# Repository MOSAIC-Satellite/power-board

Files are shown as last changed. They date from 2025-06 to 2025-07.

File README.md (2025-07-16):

# Power Board

This is the repository for MOSAIC's Power Board.

For detailed information on the Power Board, check out its core documentation [here](https://www.mosaicsat.org/core_documentation/hardware/power_board/).

To get your own MOSAIC Power Board, visit the MOSAIC fabrication guide [here](https://www.mosaicsat.org/getting_mosaic/).

## Current Features

*Newest board version: 2.0*

| **Feature** |
| :----------- |
| 6x high-side DC sensors for solar cells |
| LiPo battery high side DC sensor |
| Single-cell LiPo battery charger circuit |
| 12x  2mm JST solar cell input jacks|
| 2x 2mm JST battery input jacks |
| LiPo battery overcharge protection |
| Solar cell reverse current protection |
| 2x Qwiic connectors for I2C connection to Main Board |

## Planned Changes

The following are the current plans for changes to MOSAIC's Power Board. 

- The current version of MOSAIC's Power Board is designed to be used with only a single-cell LiPo battery like [this one](https://www.sparkfun.com/lithium-ion-battery-2ah.html). Future iterations of the Power Board should include the option to utilize different energy storage methods, such as AA and 18650 batteries. This, of course, will require a different charger circuit for each method, so the board may include a new slot where users can plug in their preferred power charger circuit. 

## Change Log

You can find the change log for the Power Board on MOSAIC's website [here](https://www.mosaicsat.org/core_documentation/hardware/power_board/change_log/).

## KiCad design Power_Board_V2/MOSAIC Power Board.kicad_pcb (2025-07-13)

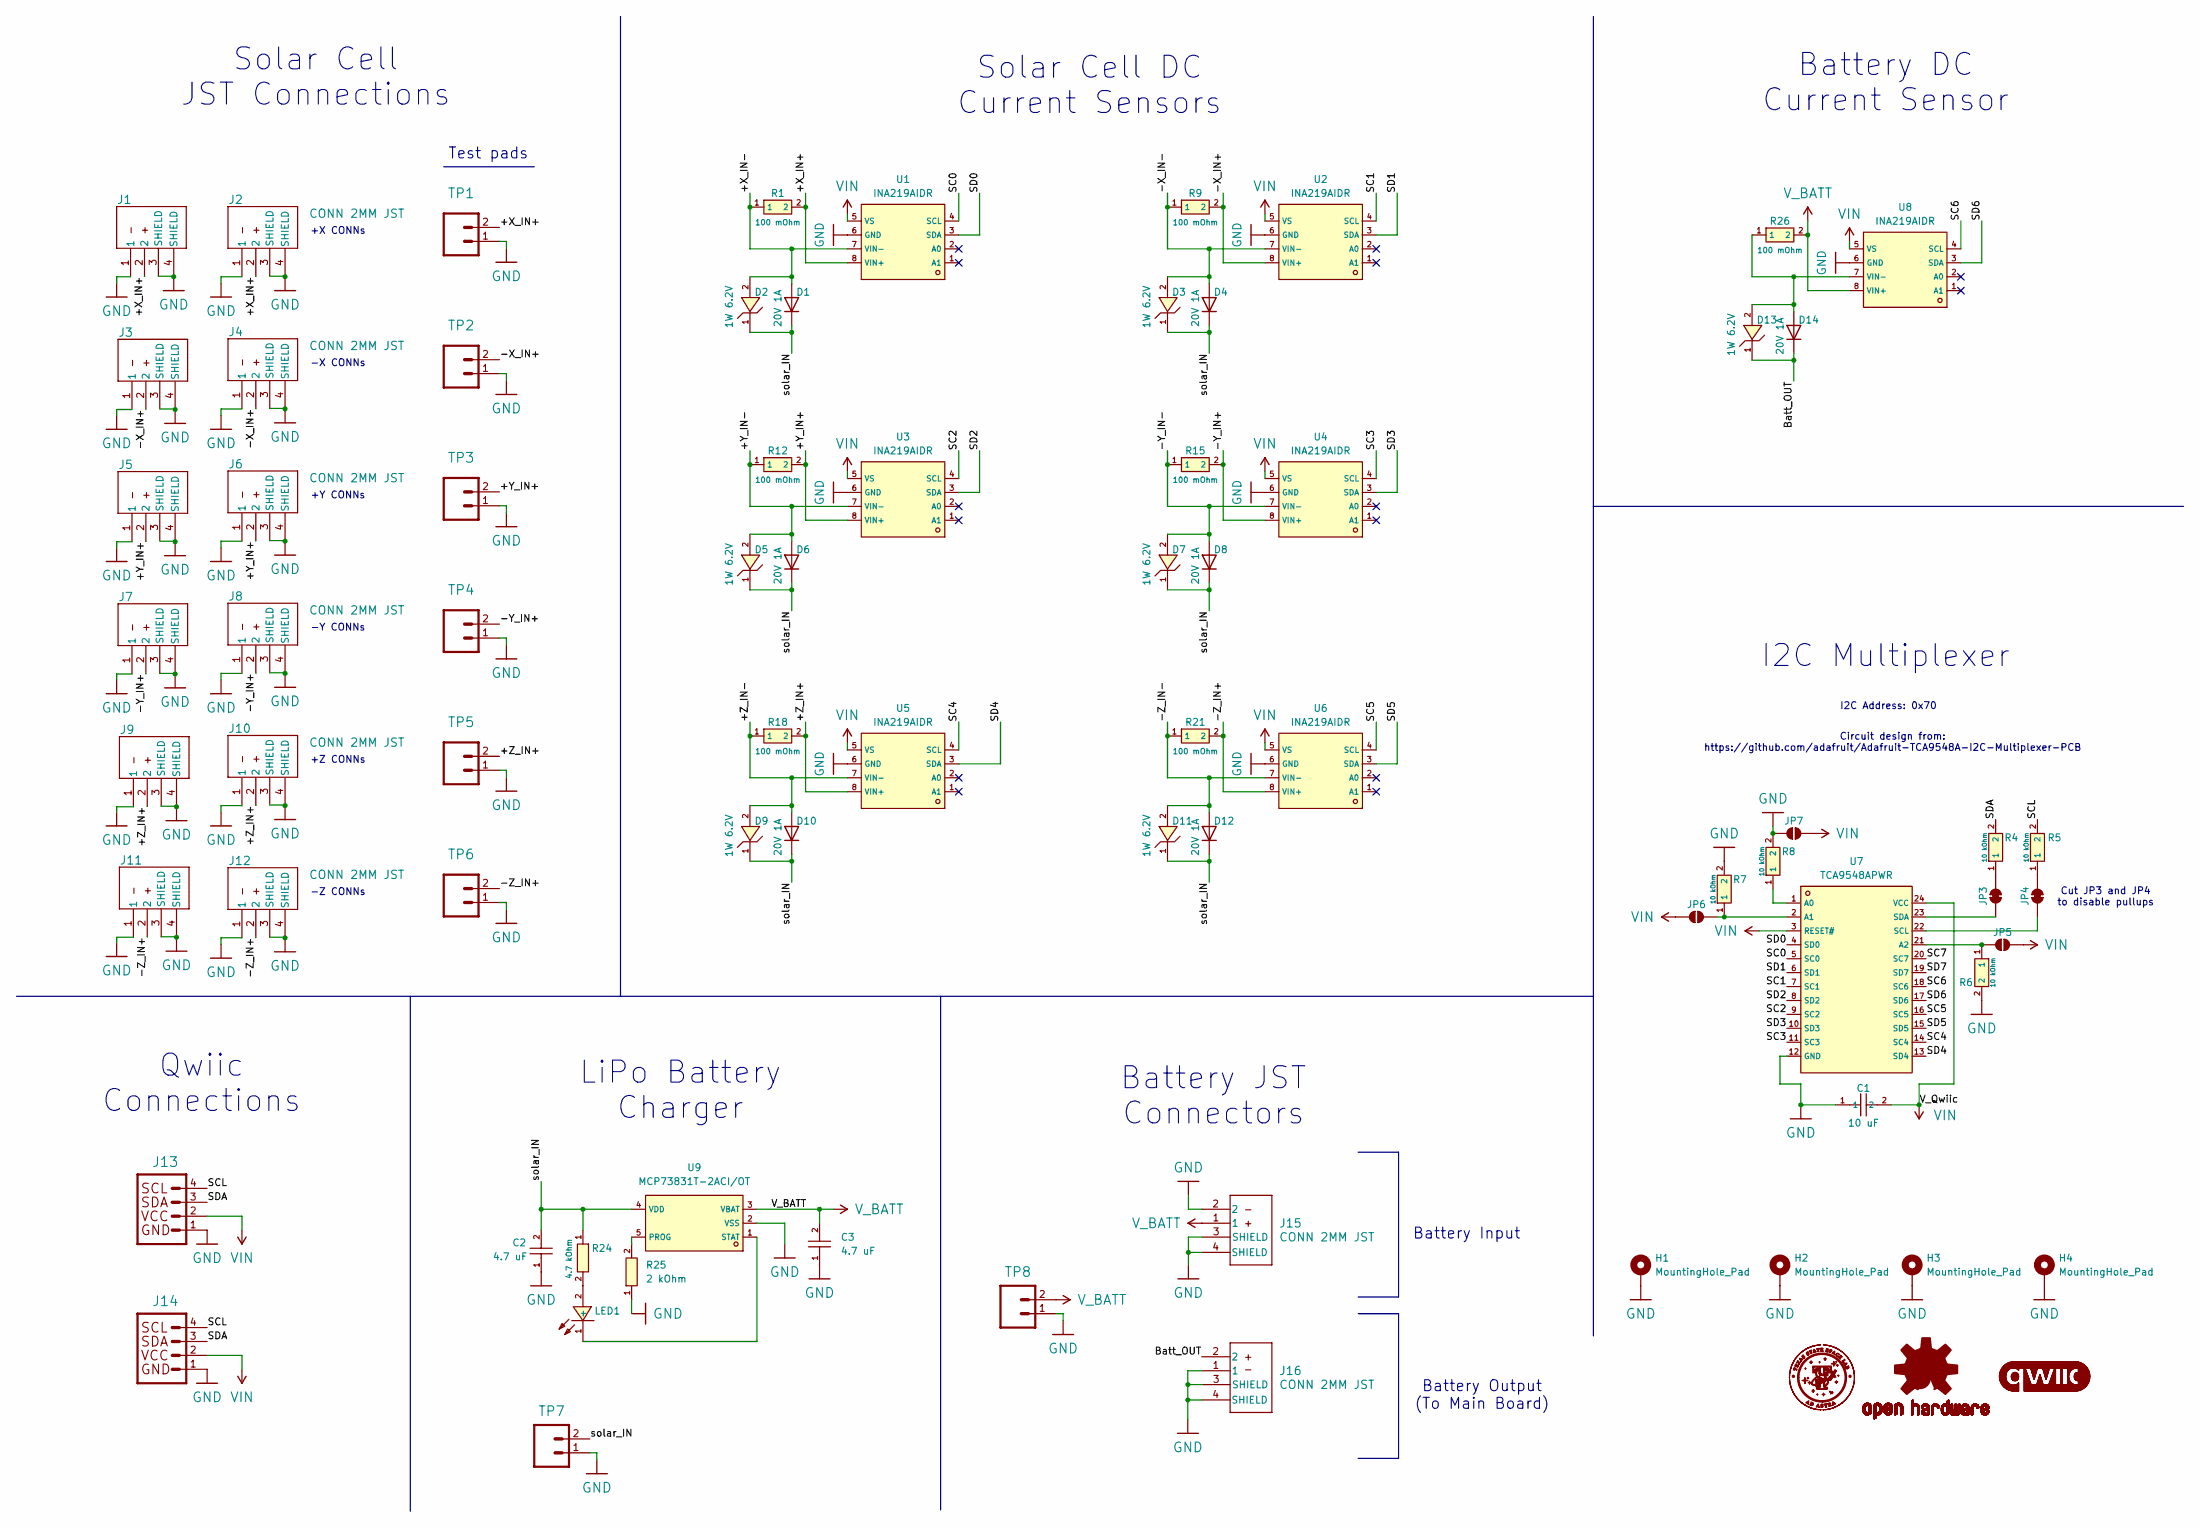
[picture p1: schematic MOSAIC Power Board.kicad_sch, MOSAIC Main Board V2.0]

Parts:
C1: 10 uF; C_0603; LCSC C1691
C2, C3: 4.7 uF; C_0603; LCSC C1705
D1, D4, D6, D8, D10, D12, D14: 20V 1A; D_SOD-323; JLCPCB Part # C41424805
D2, D3, D5, D7, D9, D11, D13: 1W 6.2V; Z_DO-214AC; LCSC C110527
H1, H2: MountingHole_Pad; MountingHole_3.2mm_Pad_Oval
H3, H4: MountingHole_Pad; MountingHole_3.2mm_M3_Pad
J1, J2, J3, J4, J5, J6, J7, J8, J9, J10, J11, J12, J15, J16: CONN 2MM JST; CONN_2mm_JST; JLCPCB Part # C295747
J13, J14: QWIIC_CONN_RA; JLCPCB Part # C145956
JP3, JP4: SolderJumper_2_Bridged; SolderJumper-2_P1.3mm_Bridged_RoundedPad1.0x1.5mm
JP5, JP6, JP7: SolderJumper_2_Open; SolderJumper-2_P1.3mm_Open_RoundedPad1.0x1.5mm
LED1: LED_0603; LCSC C125095
LOGO1: OSHW-LOGO-L
LOGO2, LOGO3: QWIIC_logo_8MM
R1, R9, R12, R15, R18, R21, R26: 100 mOhm; R_shunt; LCSC C346817
R4, R5, R6, R7, R8: 10 kOhm; R_0805; LCSC C5123591
R24: 4.7 kOhm; R_0603; LCSC C22874
R25: 2 kOhm; R_0603; LCSC C22975
TP1, TP2, TP3, TP4, TP5, TP6, TP7, TP8: 1X02_NO_SILK
U1, U2, U3, U4, U5, U6, U8: INA219AIDR; LCSC C138706
U7: TCA9548APWR; LCSC C130026
U9: MCP73831T-2ACI/OT; MCP73831_IC_BATT_CNTL; LCSC C424093

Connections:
/+X_IN+: J1.2, J2.2, R1.2, TP1.2, U1.8 (VIN+)
/+X_IN-: D1.2 (A), D2.2, R1.1, U1.7 (VIN-)
/+Y_IN+: J5.2, J6.2, R12.2, TP3.2, U3.8 (VIN+)
/+Y_IN-: D5.2, D6.2 (A), R12.1, U3.7 (VIN-)
/+Z_IN+: J9.2, J10.2, R18.2, TP5.2, U5.8 (VIN+)
/+Z_IN-: D9.2, D10.2 (A), R18.1, U5.7 (VIN-)
/-X_IN+: J3.2, J4.2, R9.2, TP2.2, U2.8 (VIN+)
/-X_IN-: D3.2, D4.2 (A), R9.1, U2.7 (VIN-)
/-Y_IN+: J7.2, J8.2, R15.2, TP4.2, U4.8 (VIN+)
/-Y_IN-: D7.2, D8.2 (A), R15.1, U4.7 (VIN-)
/-Z_IN+: J11.2, J12.2, R21.2, TP6.2, U6.8 (VIN+)
/-Z_IN-: D11.2, D12.2 (A), R21.1, U6.7 (VIN-)
/Batt_OUT: D13.1, D14.1 (K), J16.2
/SC0: U1.4 (SCL), U7.5 (SC0)
/SC1: U2.4 (SCL), U7.7 (SC1)
/SC2: U3.4 (SCL), U7.9 (SC2)
/SC3: U4.4 (SCL), U7.11 (SC3)
/SC4: U5.4 (SCL), U7.14 (SC4)
/SC5: U6.4 (SCL), U7.16 (SC5)
/SC6: U7.18 (SC6), U8.4 (SCL)
/SC7: U7.20 (SC7)
/SCL: J13.4, J14.4, R5.2
/SD0: U1.3 (SDA), U7.4 (SD0)
/SD1: U2.3 (SDA), U7.6 (SD1)
/SD2: U3.3 (SDA), U7.8 (SD2)
/SD3: U4.3 (SDA), U7.10 (SD3)
/SD4: U5.3 (SDA), U7.13 (SD4)
/SD5: U6.3 (SDA), U7.15 (SD5)
/SD6: U7.17 (SD6), U8.3 (SDA)
/SD7: U7.19 (SD7)
/SDA: J13.3, J14.3, R4.2
/solar_IN: C2.2, D1.1 (K), D2.1, D3.1, D4.1 (K), D5.1, D6.1 (K), D7.1, D8.1 (K), D9.1, D10.1 (K), D11.1, D12.1 (K), R24.1, TP7.2, U9.4 (VDD)
GND: C1.1, C2.1, C3.1, H1.1, H2.1, H3.1, H4.1, J1.1, J1.3 (SHIELD), J1.4 (SHIELD), J2.1, J2.3 (SHIELD), J2.4 (SHIELD), J3.1, J3.3 (SHIELD), J3.4 (SHIELD), J4.1, J4.3 (SHIELD), J4.4 (SHIELD), J5.1, J5.3 (SHIELD), J5.4 (SHIELD), J6.1, J6.3 (SHIELD), J6.4 (SHIELD), J7.1, J7.3 (SHIELD), J7.4 (SHIELD), J8.1, J8.3 (SHIELD), J8.4 (SHIELD), J9.1, J9.3 (SHIELD), J9.4 (SHIELD), J10.1, J10.3 (SHIELD), J10.4 (SHIELD), J11.1, J11.3 (SHIELD), J11.4 (SHIELD), J12.1, J12.3 (SHIELD), J12.4 (SHIELD), J13.1, J14.1, J15.2, J15.3 (SHIELD), J15.4 (SHIELD), J16.1, J16.3 (SHIELD), J16.4 (SHIELD), JP7.1 (A), R6.2, R7.2, R8.2, R25.1, TP1.1, TP2.1, TP3.1, TP4.1, TP5.1, TP6.1, TP7.1, TP8.1, U1.6 (GND), U2.6 (GND), U3.6 (GND), U4.6 (GND), U5.6 (GND), U6.6 (GND), U7.12 (GND), U8.6 (GND), U9.2 (VSS)
unnamed: D13.2, D14.2 (A), R26.1, U8.7 (VIN-)
unnamed: JP3.1 (A), U7.23 (SDA)
unnamed: JP3.2 (B), R4.1
unnamed: JP4.1 (A), U7.22 (SCL)
unnamed: JP4.2 (B), R5.1
unnamed: JP5.1 (A), R6.1, U7.21 (A2)
unnamed: JP6.2 (B), R7.1, U7.2 (A1)
unnamed: LED1.2 (+), R24.2
unnamed: LED1.1 (-), U9.1 (STAT)
unnamed: R8.1, U7.1 (A0)
unnamed: R25.2, U9.5 (PROG)
VIN: C1.2, J13.2, J14.2, JP5.2 (B), JP6.1 (A), JP7.2 (B), U1.5 (VS), U2.5 (VS), U3.5 (VS), U4.5 (VS), U5.5 (VS), U6.5 (VS), U7.3 (RESET#), U7.24 (VCC), U8.5 (VS)
V_BATT: C3.2, J15.1, R26.2, TP8.2, U8.8 (VIN+), U9.3 (VBAT)

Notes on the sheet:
Battery Input
-Z CONNs
Battery JST Connectors
Solar Cell JST Connections
Test pads
I2C Multiplexer
-Y CONNs
Circuit design from: https://github.com/adafruit/Adafruit-TCA9548A-I2C-Multiplexer-PCB
+Z CONNs
Battery DC Current Sensor
Qwiic Connections
+X CONNs
+Y CONNs
I2C Address: 0x70
Cut JP3 and JP4 to disable pullups
LiPo Battery Charger
-X CONNs
Battery Output (To Main Board)
Solar Cell DC Current Sensors

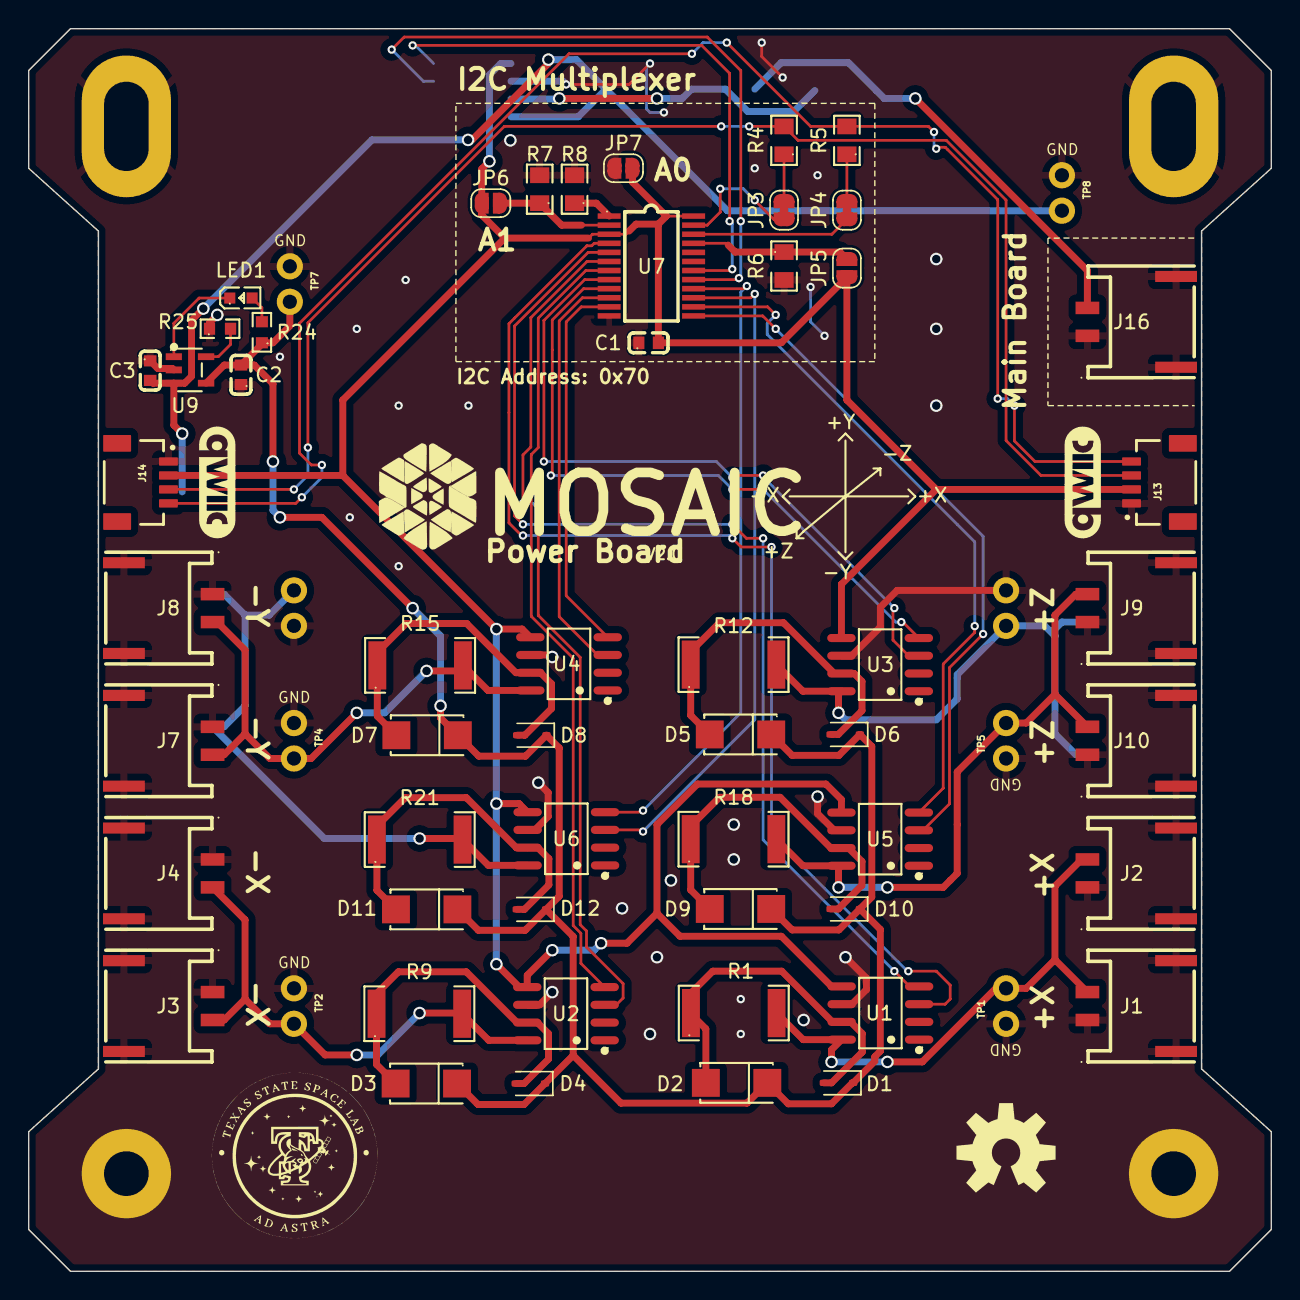
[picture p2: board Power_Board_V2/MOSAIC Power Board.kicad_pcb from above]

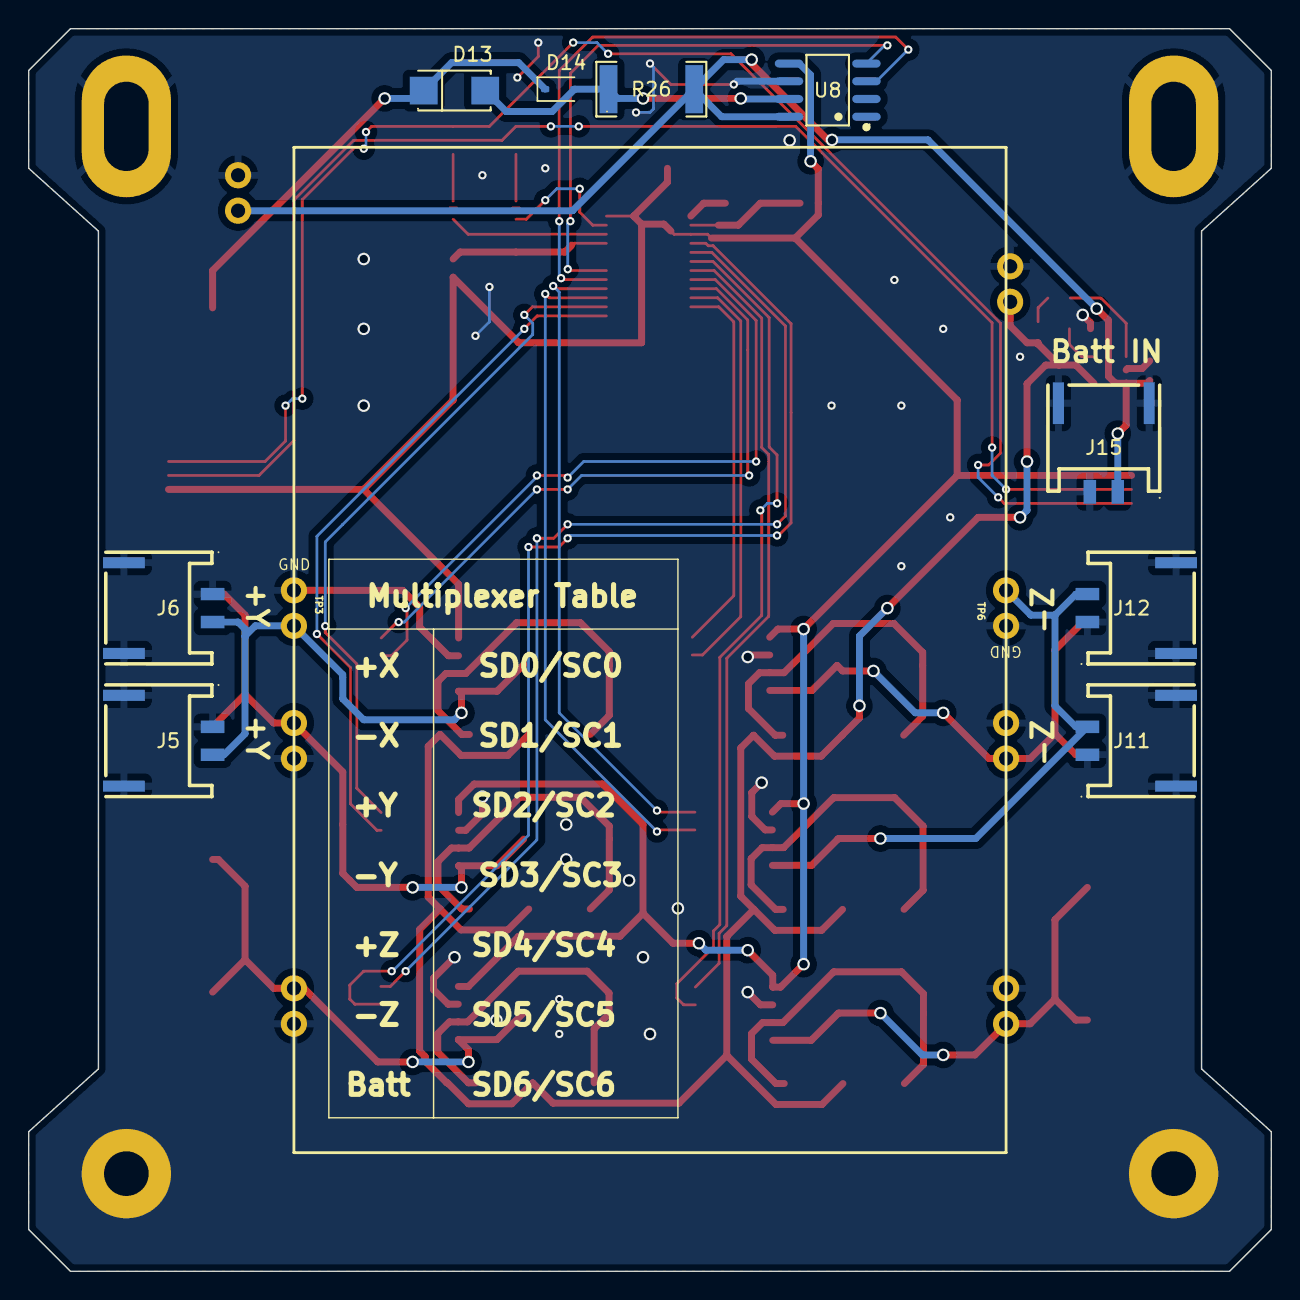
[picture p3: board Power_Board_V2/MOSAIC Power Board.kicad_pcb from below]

Board: 2 copper layers, 89.0 x 89.0 mm, 77 parts (11 on the bottom side), 44 nets.

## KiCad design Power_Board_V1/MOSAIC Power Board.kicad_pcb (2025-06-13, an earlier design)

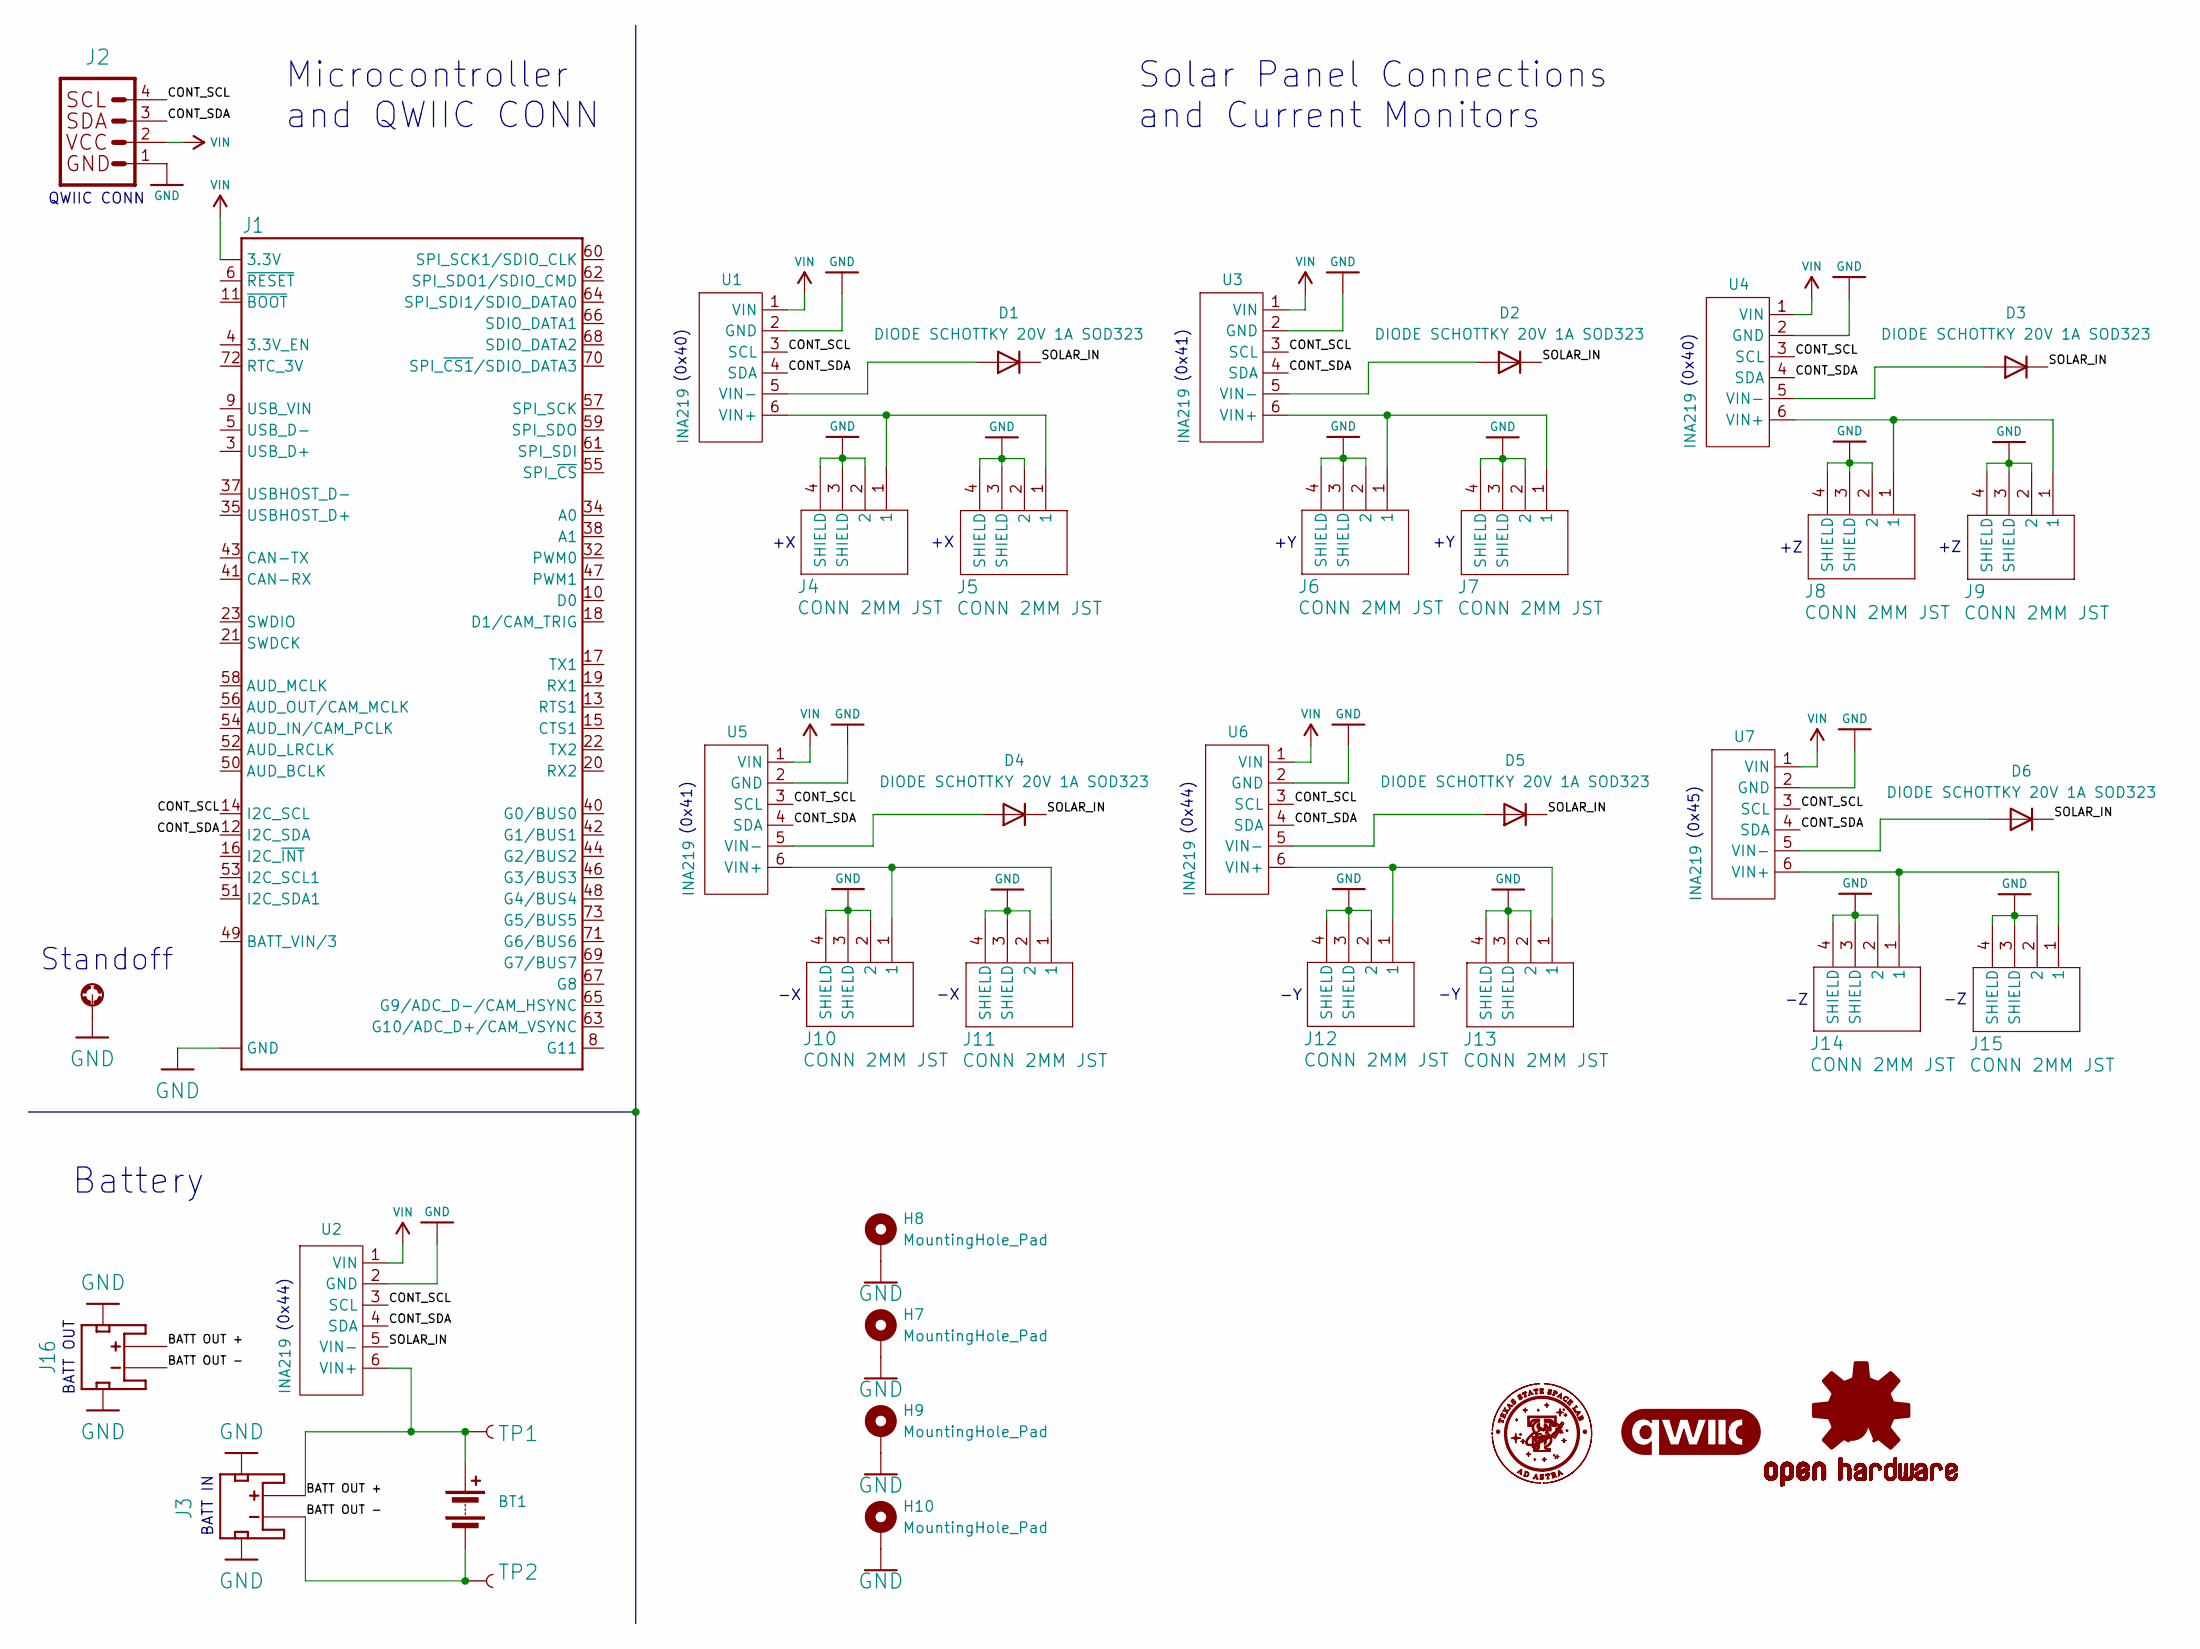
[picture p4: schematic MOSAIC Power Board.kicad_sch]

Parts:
BT1: Battery; SparkFun Lithium Ion Battery - 2Ah
D1, D2, D3, D4, D5, D6: DIODE SCHOTTKY 20V 1A SOD323; D_SOD-323; JLCPCB Part # C435857
H1: STAND-OFF-REFLOW-M2.5
H7, H8: MountingHole_Pad; MountingHole_3.2mm_M3_Pad
H9, H10: MountingHole_Pad; MountingHole_3.2mm_Pad_Oval
J1: CONN E; M.2-CONNECTOR-E; JLCPCB Part # C2977809
J2: CONN_QWIIC; JST04_1MM_RA; JLCPCB Part # C145956
J3, J16: CONN_JST_BATT; JST-2-SMD
J4, J5, J6, J7, J8, J9, J10, J11, J12, J13, J14, J15: CONN 2MM JST; CONN_S2B-PH-SM4-TB_JST; JLCPCB Part # C295747
LOGO1: OSHW-LOGO-L
LOGO2: QWIIC_8MM
TP1, TP2: PAD.03X.05
U1, U2, U3, U4, U5, U6, U7: INA219; INA219 Breakout

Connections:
/BATT OUT +: BT1.1 (+), J3.2 (+), J16.2 (+), TP1.1, U2.6 (VIN+)
/BATT OUT -: BT1.2 (-), J3.1 (-), J16.1 (-), TP2.1
/CONT_SCL: J1.14 (I2C_SCL), J2.4, U1.3 (SCL), U2.3 (SCL), U3.3 (SCL), U4.3 (SCL), U5.3 (SCL), U6.3 (SCL), U7.3 (SCL)
/CONT_SDA: J1.12 (I2C_SDA), J2.3, U1.4 (SDA), U2.4 (SDA), U3.4 (SDA), U4.4 (SDA), U5.4 (SDA), U6.4 (SDA), U7.4 (SDA)
/SOLAR_IN: D1.1 (K), D2.1 (K), D3.1 (K), D4.1 (K), D5.1 (K), D6.1 (K), U2.5 (VIN-)
GND: H1.1, H7.1, H8.1, H9.1, H10.1, J1.1 (GND), J1.7 (GND), J1.33 (GND), J1.36 (GND), J1.39 (GND), J1.45 (GND), J1.75 (GND), J2.1, J3.NC1 (PAD1), J3.NC2 (PAD2), J4.2, J4.3 (SHIELD), J4.4 (SHIELD), J5.2, J5.3 (SHIELD), J5.4 (SHIELD), J6.2, J6.3 (SHIELD), J6.4 (SHIELD), J7.2, J7.3 (SHIELD), J7.4 (SHIELD), J8.2, J8.3 (SHIELD), J8.4 (SHIELD), J9.2, J9.3 (SHIELD), J9.4 (SHIELD), J10.2, J10.3 (SHIELD), J10.4 (SHIELD), J11.2, J11.3 (SHIELD), J11.4 (SHIELD), J12.2, J12.3 (SHIELD), J12.4 (SHIELD), J13.2, J13.3 (SHIELD), J13.4 (SHIELD), J14.2, J14.3 (SHIELD), J14.4 (SHIELD), J15.2, J15.3 (SHIELD), J15.4 (SHIELD), J16.NC1 (PAD1), J16.NC2 (PAD2), U1.2 (GND), U2.2 (GND), U3.2 (GND), U4.2 (GND), U5.2 (GND), U6.2 (GND), U7.2 (GND)
unnamed: D1.2 (A), U1.5 (VIN-)
unnamed: D2.2 (A), U3.5 (VIN-)
unnamed: D3.2 (A), U4.5 (VIN-)
unnamed: D4.2 (A), U5.5 (VIN-)
unnamed: D5.2 (A), U6.5 (VIN-)
unnamed: D6.2 (A), U7.5 (VIN-)
unnamed: J4.1, J5.1, U1.6 (VIN+)
unnamed: J6.1, J7.1, U3.6 (VIN+)
unnamed: J8.1, J9.1, U4.6 (VIN+)
unnamed: J10.1, J11.1, U5.6 (VIN+)
unnamed: J12.1, J13.1, U6.6 (VIN+)
unnamed: J14.1, J15.1, U7.6 (VIN+)
VIN: J1.2 (3.3V), J1.74 (3.3V), J2.2, U1.1 (VIN), U2.1 (VIN), U3.1 (VIN), U4.1 (VIN), U5.1 (VIN), U6.1 (VIN), U7.1 (VIN)

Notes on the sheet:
(0x41)
(0x44)
QWIIC CONN
(0x40)
Microcontroller and QWIIC CONN
Solar Panel Connections and Current Monitors
(0x45)
Battery
BATT OUT
BATT IN
Standoff

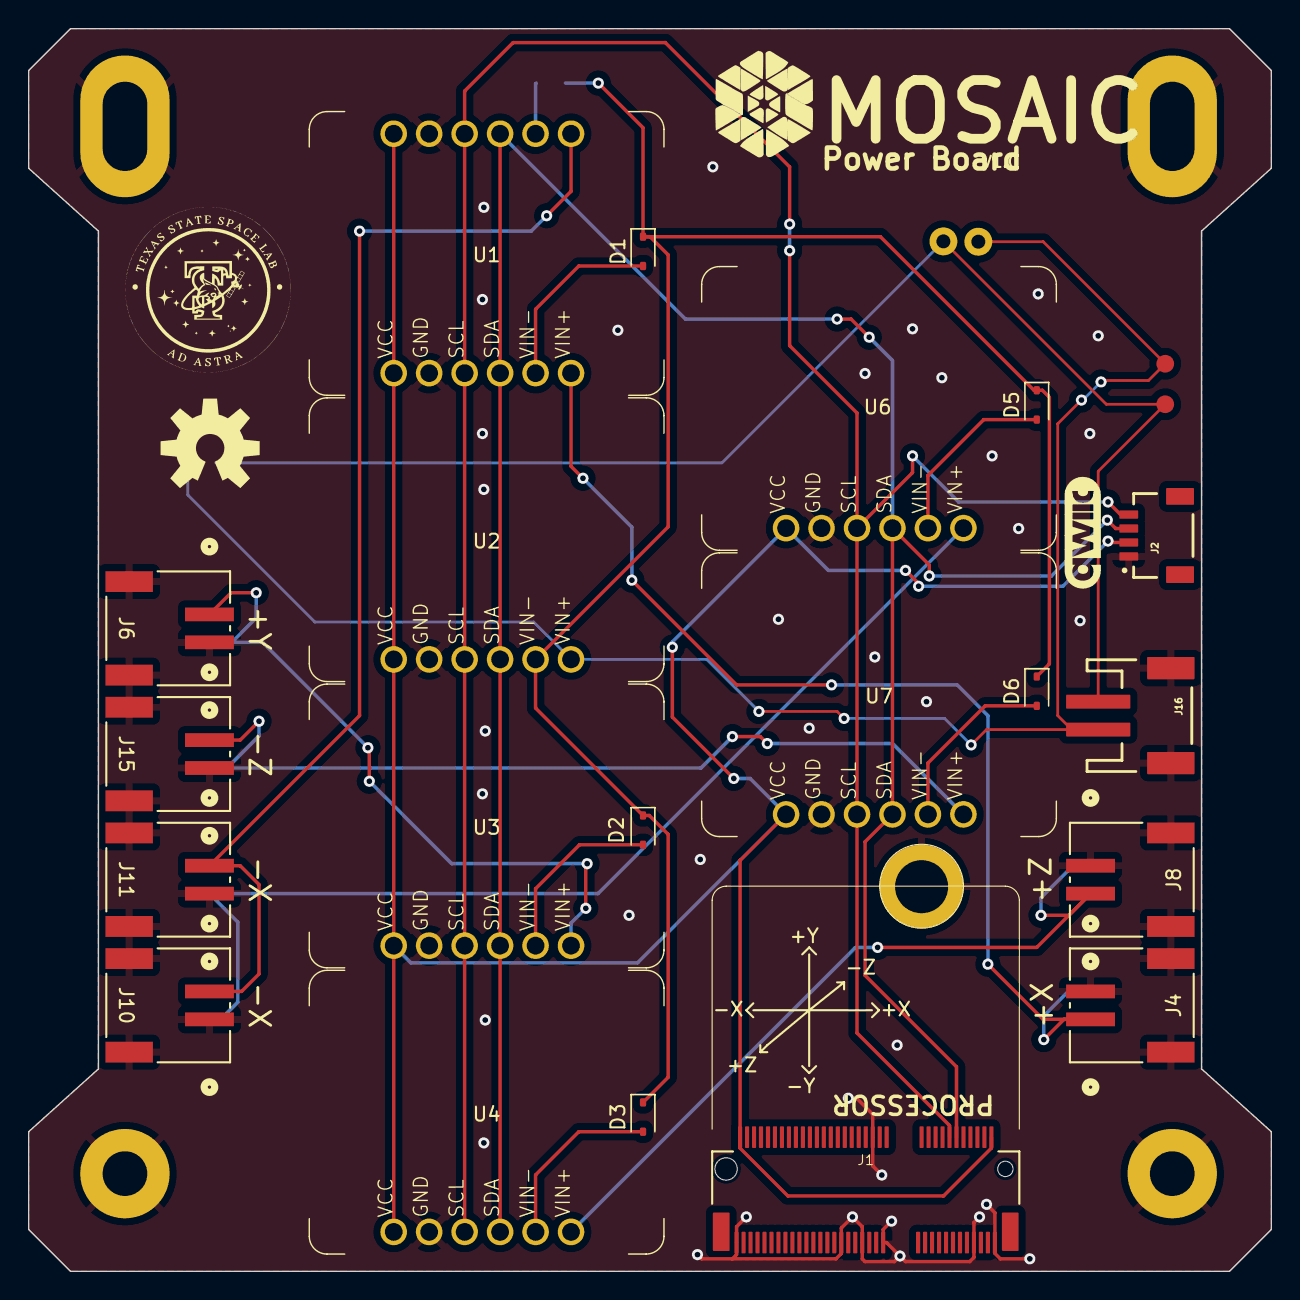
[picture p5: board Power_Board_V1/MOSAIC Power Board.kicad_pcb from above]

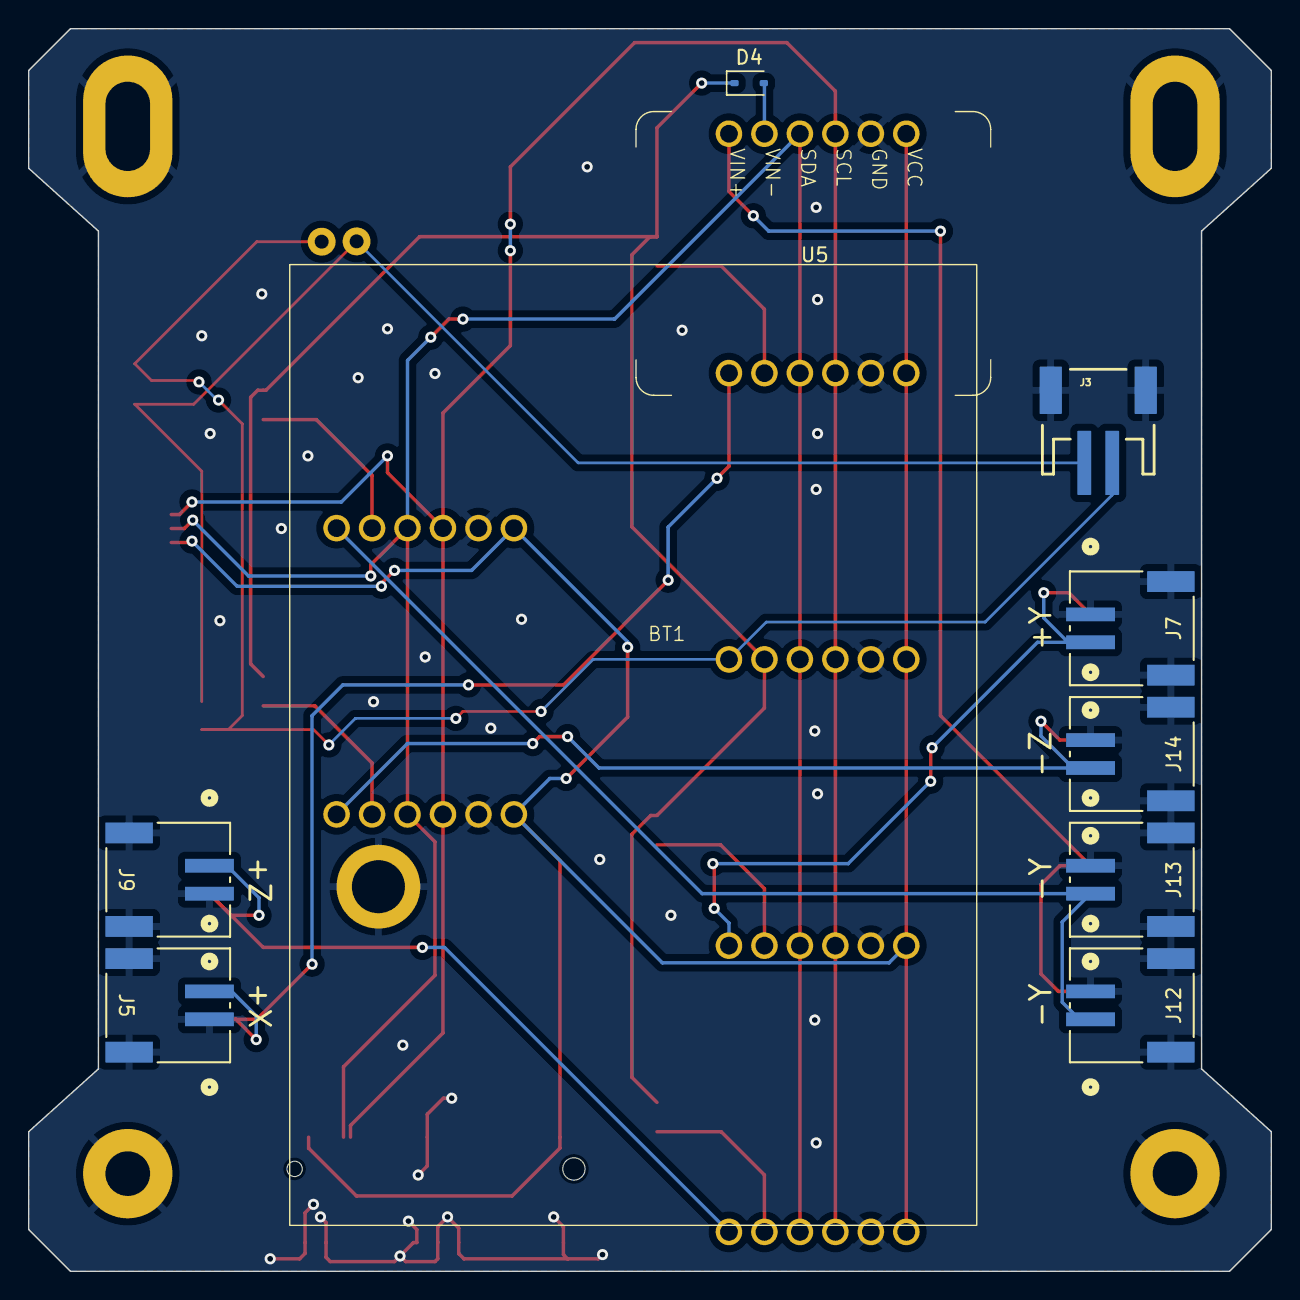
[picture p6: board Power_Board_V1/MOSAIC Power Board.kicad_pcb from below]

Board: 2 copper layers, 89.0 x 89.0 mm, 39 parts (10 on the bottom side), 19 nets.

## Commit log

2024-08-07 Create LICENSE.txt
    Created file for non-software copyright license for the Power Board repository for MOSAIC.
2024-08-07 Initial Upload
    Initial upload of files for the MOSAIC Power Board repository.
    [MOSAIC Power Board.kicad_pcb, MOSAIC Power Board.kicad_sch]
2025-04-29 Generated a new BOM
2025-04-29 saved changes
    [MOSAIC Power Board.kicad_pcb]
2025-04-29 Updated J3, J16 sources
    [MOSAIC Power Board.kicad_sch]
2025-04-29 Updatd J2 Source
    [MOSAIC Power Board.kicad_sch]
2025-05-30 Work on fixing libraries
    [MOSAIC Power Board.kicad_sch]
2025-05-30 More fixing of libraries
    [MOSAIC Power Board.kicad_pcb, MOSAIC Power Board.kicad_sch]
2025-06-10 Placement and routing work
    [MOSAIC Power Board.kicad_pcb, MOSAIC Power Board.kicad_sch]
2025-06-12 Finished placement and tracing
    [MOSAIC Power Board.kicad_pcb, MOSAIC Power Board.kicad_sch]
2025-06-12 Sourced parts at JLCPCB
    [MOSAIC Power Board.kicad_sch]
2025-06-13 Made JLCPCB production files
    [MOSAIC Power Board.kicad_pcb, MOSAIC Power Board.kicad_sch]
2025-07-07 updated i2c addresses for ina219s
    [MOSAIC Power Board.kicad_sch]
2025-07-11 started v2.0
    [MOSAIC Power Board.kicad_pcb, MOSAIC Power Board.kicad_sch]
2025-07-11 work on schematic
    [MOSAIC Power Board.kicad_sch]
2025-07-11 Finished session
    [MOSAIC Power Board.kicad_pcb]
2025-07-11 worked on schematic
    [MOSAIC Power Board.kicad_sch]
2025-07-12 work on pcb positioning
    [MOSAIC Power Board.kicad_pcb, MOSAIC Power Board.kicad_sch]
2025-07-13 routing work
    [MOSAIC Power Board.kicad_pcb, MOSAIC Power Board.kicad_sch]
2025-07-13 finished v2.0
    [MOSAIC Power Board.kicad_pcb, MOSAIC Power Board.kicad_sch]
2026-01-09 Updated to replace out of stock comps.
    Zener diodes were out of stock with JLCPCB. Updated production folder to include replacement components.

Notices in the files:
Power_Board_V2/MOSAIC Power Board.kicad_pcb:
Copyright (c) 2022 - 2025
